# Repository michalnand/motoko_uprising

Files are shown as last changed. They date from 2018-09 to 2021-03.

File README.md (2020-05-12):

# Motoko Uprising
## line following robot with neural network predictor

Advanced line following robot, using custom deep neural network for curve shape prediction.
Robot can recognize straight line and speed up.

* Video1 of woking robot [motoko video 1](https://www.youtube.com/watch?v=E9FJIDowNmU)
* Video2 of woking robot [motoko video 2](https://www.youtube.com/watch?v=xUAJ1LA6Xwc)

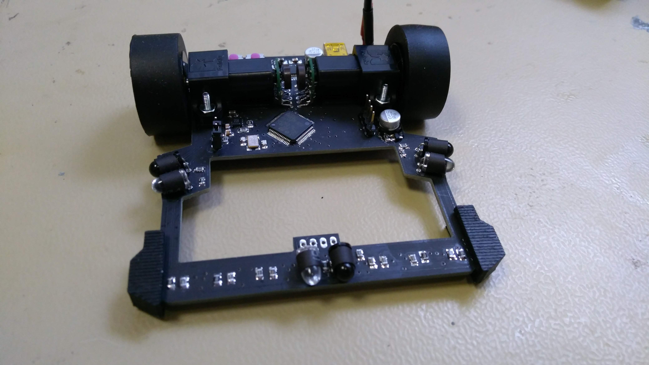
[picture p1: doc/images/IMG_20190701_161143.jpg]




## hardware

* CPU is ARM Cortex M4F, stm32f303, 72MHz
  * with simd instructions, good to have for deep learning
* gyroscope : lsm303 
  * (or something like THAT - yeah, they are changing it more often then socks)
* motors : pololu HP 1:30, micro metal gear, with magnetic encoders
* motor driver : TI DRV8834
* line sensors : phototransitors for visible light (not IR)
  * Iam using white leds, so the line can be colored - not only black
* obstacle detection :
  * common IR leds, and laser (still not working as I wish - too slow, but high range)
* accu : LiPol 2S, 150mAh, from dualsky

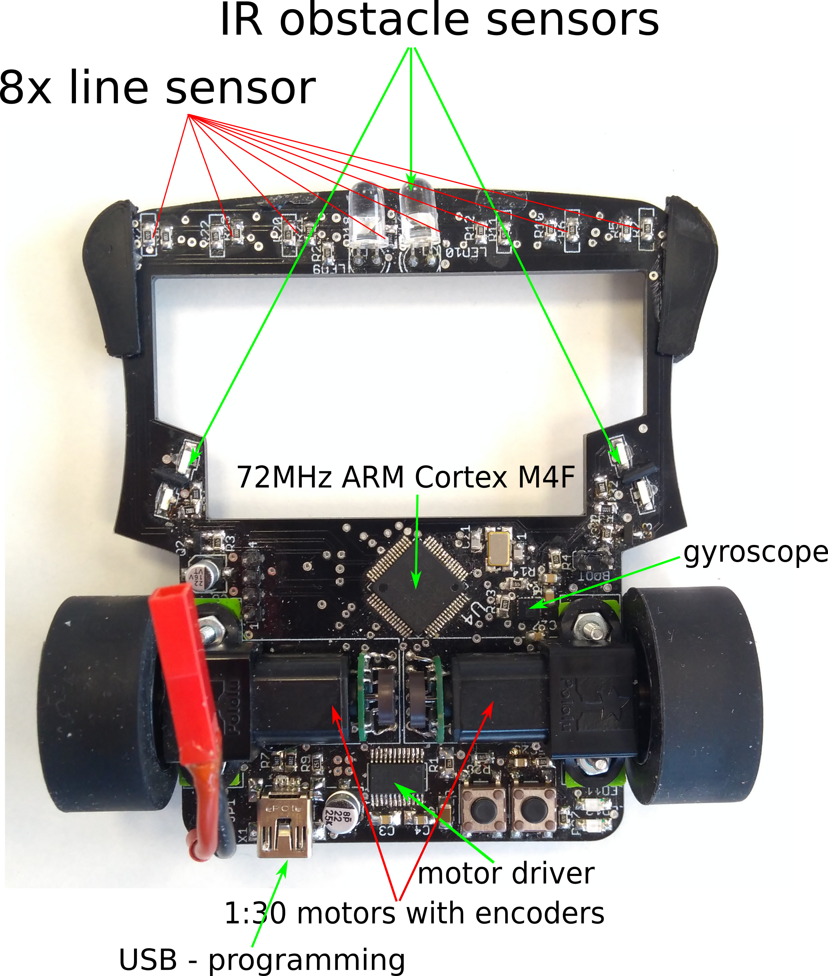
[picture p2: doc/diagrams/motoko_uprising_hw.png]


Some photos from mounting this devilry device :
* PCB design are in  [pcb](hardware/export), ready to send to your favorite manufactor
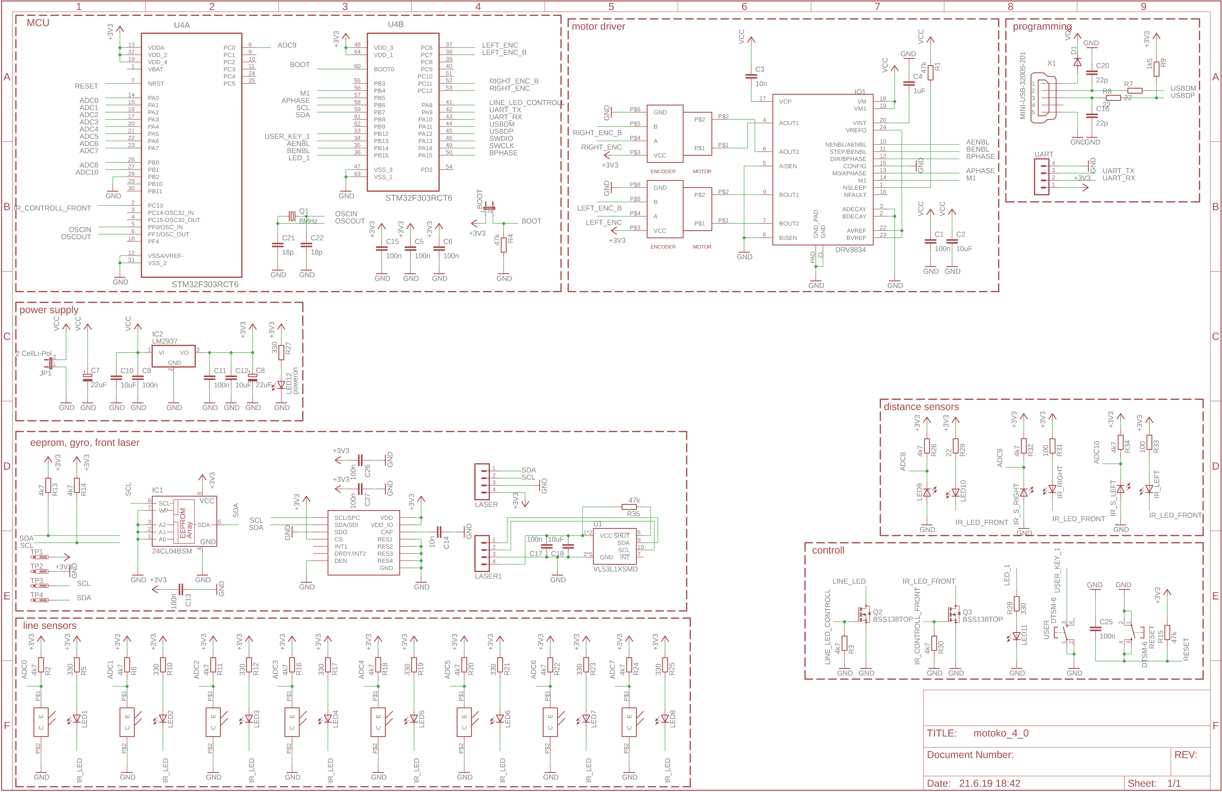
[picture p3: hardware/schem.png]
  * 
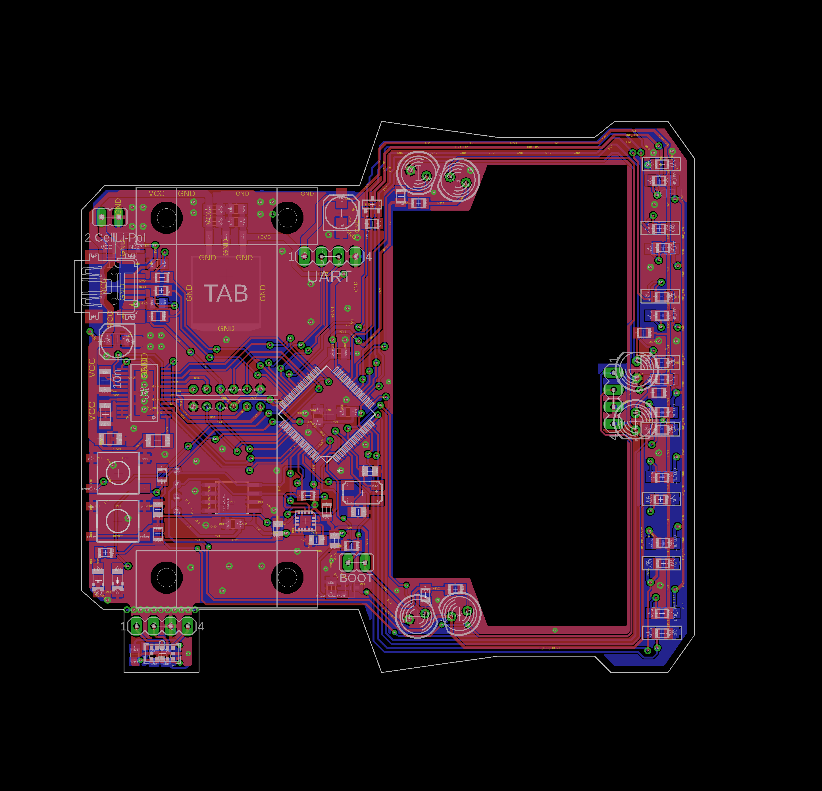
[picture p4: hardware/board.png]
  * 
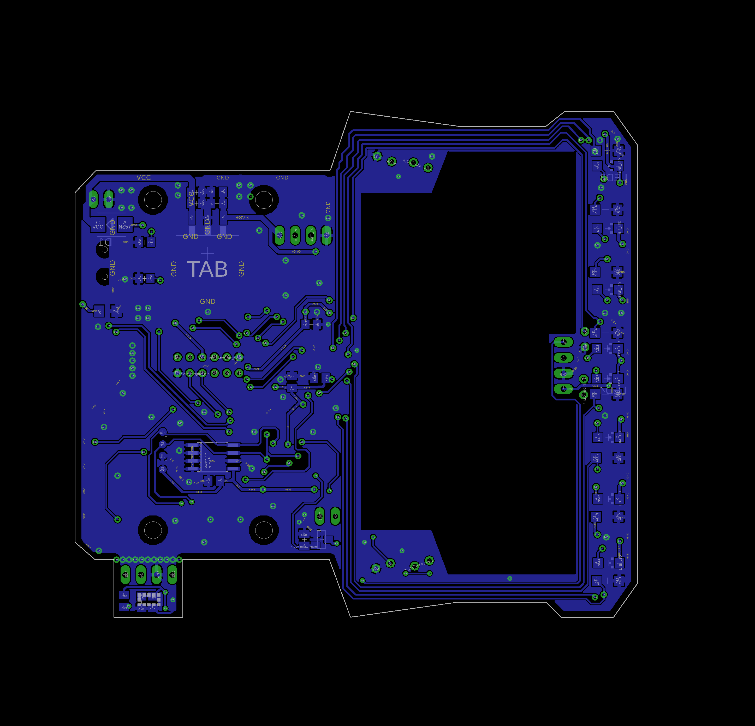
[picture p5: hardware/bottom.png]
  * 
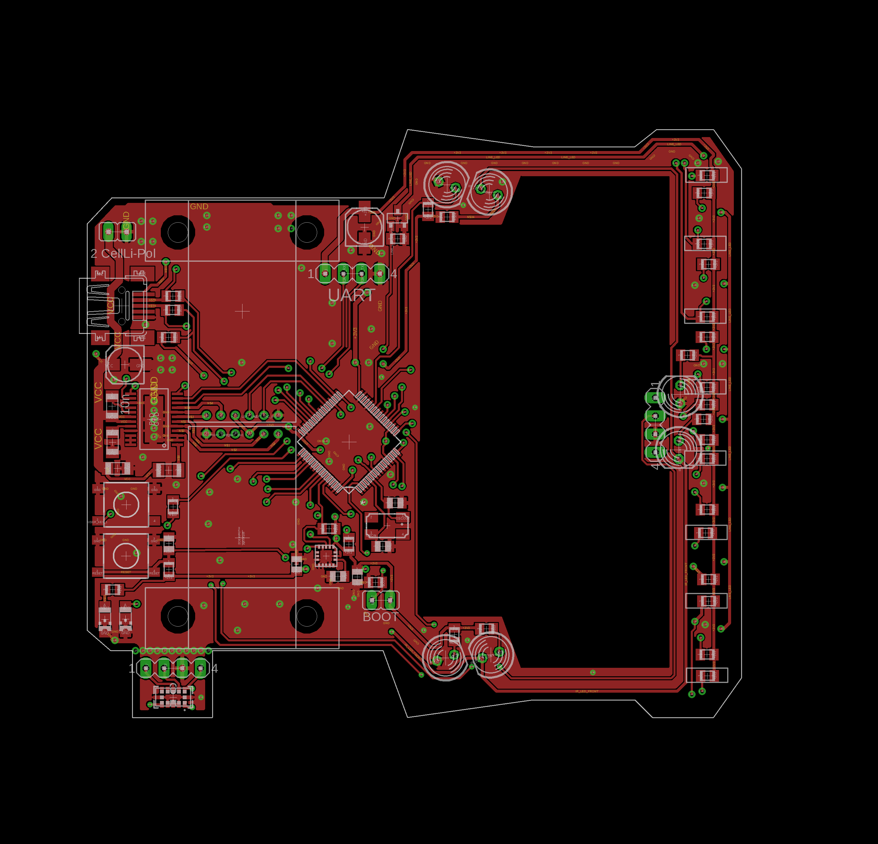
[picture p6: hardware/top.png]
  * 
  
* Chassis, there are little of 3D printed parts [3d print](hardware/chassis)
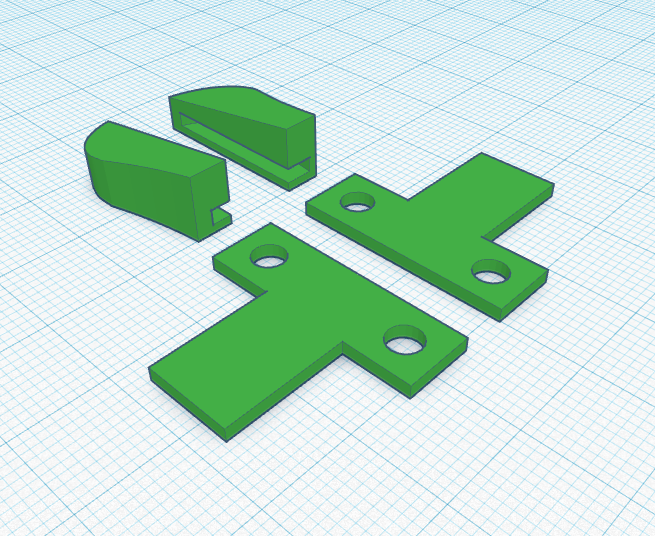
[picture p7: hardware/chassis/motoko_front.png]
  * 

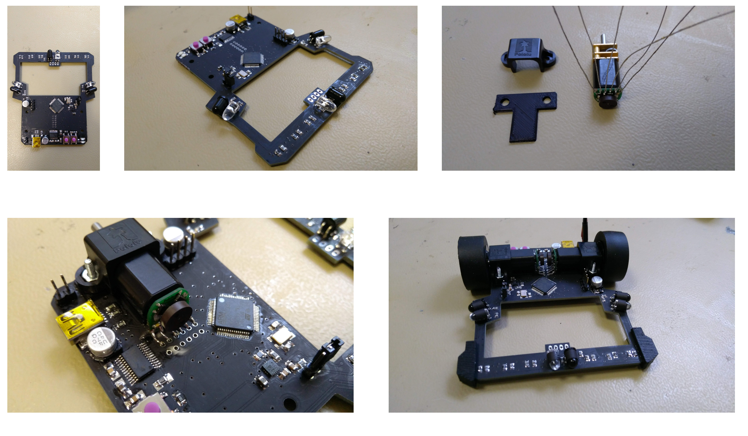
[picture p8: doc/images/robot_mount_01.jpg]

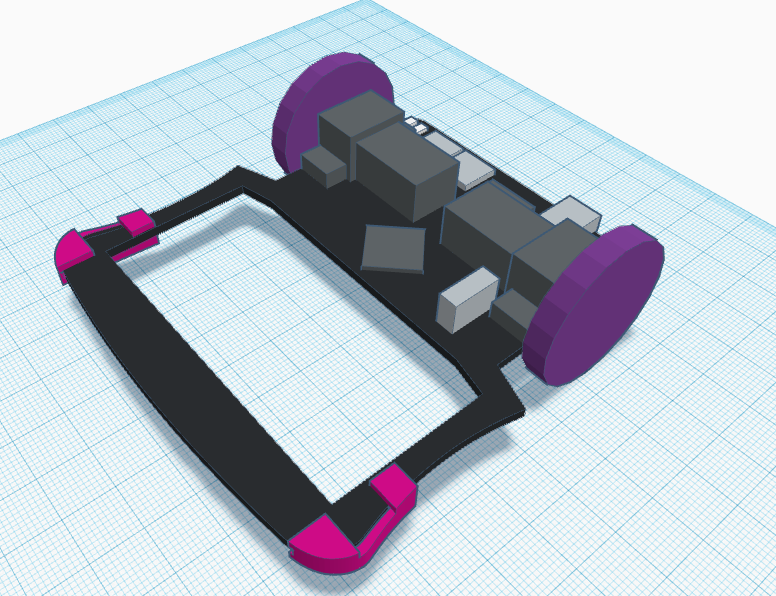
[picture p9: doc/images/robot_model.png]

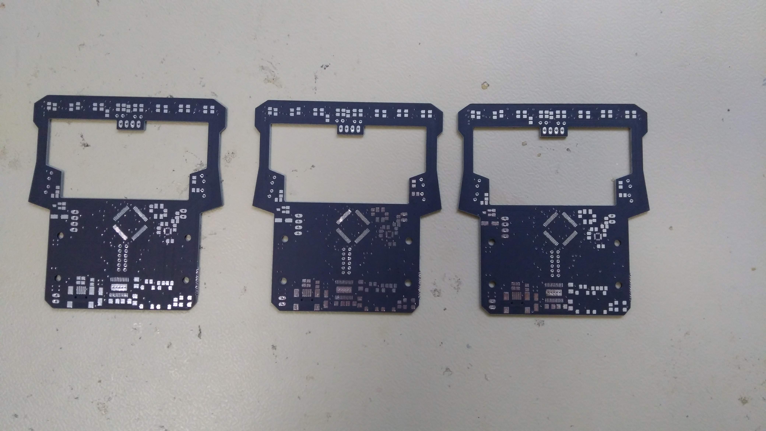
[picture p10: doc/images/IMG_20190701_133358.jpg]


## firmware

### control loops

* ADC reads line sensor, using quadratic interpolation for precission line position estimation
* for steering PD controller is used
* for motor controll two PIDs are used (data from encoders are filtered by low pass filters)
* target speed is estimated by neural network, using line shape classification

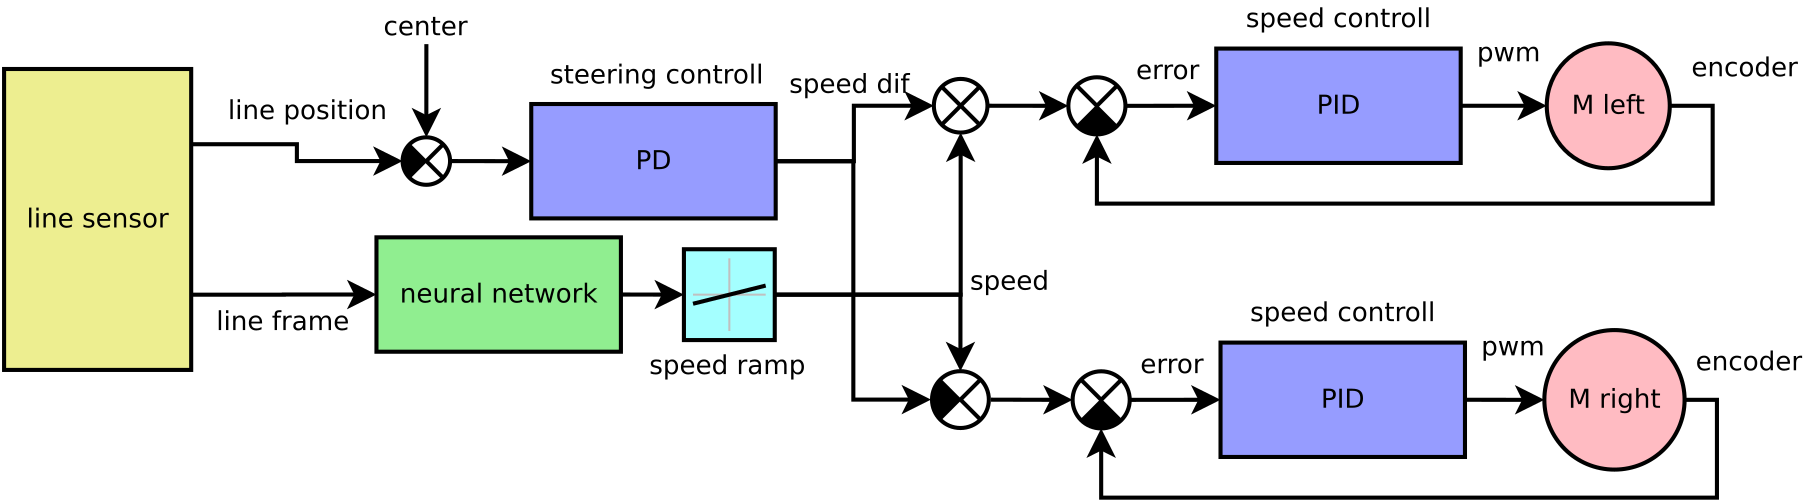
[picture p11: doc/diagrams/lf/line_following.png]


### neural network

tiny convolutional neural network is used, with architecture :
IN1x8x8 - C4x3x3 - P2x2 - C8x3x3 - P2x2 - FC5

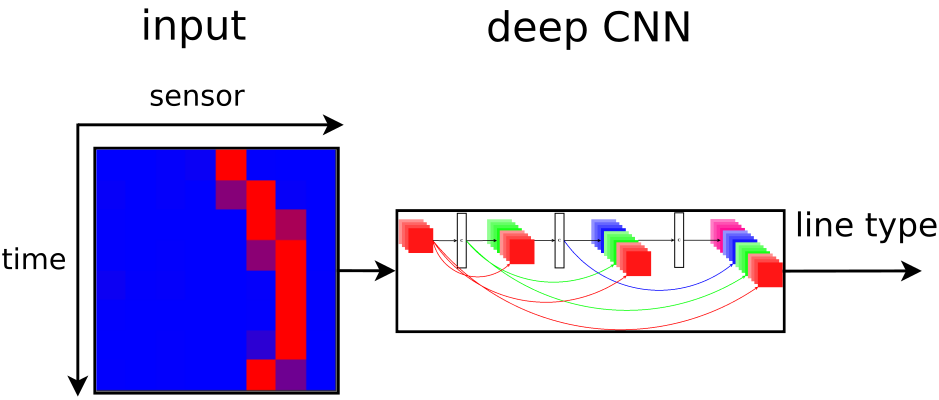
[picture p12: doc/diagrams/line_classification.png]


the custom embedded CNN framework is used

```cpp
LineNetwork::LineNetwork()
			:EmbeddedNet()
{
  input_shape.w = 8;
  input_shape.h = 8;
  input_shape.d = 1;

  output_shape.w = 1;
  output_shape.h = 1; 
  output_shape.d = 5;

  layers[0] = new EmbeddedNetConvolutionLayer(layer_0_shape,layer_0_input_shape,layer_0_output_shape,layer_0_weights,layer_0_bias,layer_0_weights_range,layer_0_bias_range);
  layers[1] = new EmbeddedNetMaxPoolingLayer(layer_1_shape,layer_1_input_shape,layer_1_output_shape);
  layers[2] = new EmbeddedNetConvolutionLayer(layer_2_shape,layer_2_input_shape,layer_2_output_shape,layer_2_weights,layer_2_bias,layer_2_weights_range,layer_2_bias_range);
  layers[3] = new EmbeddedNetMaxPoolingLayer(layer_3_shape,layer_3_input_shape,layer_3_output_shape);
  layers[4] = new EmbeddedNetFcLayer(layer_4_shape,layer_4_input_shape,layer_4_output_shape,layer_4_weights,layer_4_bias,layer_4_weights_range,layer_4_bias_range);

  layers_count = 5;
  allocate_buffer();
}
```

### PIDs

PIDs in differential form are used, with antiwindup and derivation kick avoid trick

the controller equation is :
u(n) = u(n-1) + k_0e(n) + k_1e(n-1) + k_2e(n-2)

where
* e(n) is error
* u(n) is controller output
* k0 = kp + ki + kd
* k1 = -kp     -2kd
* k2 = kd

```cpp
float PID::process(float error, float plant_output)
{
    e1 = e0;
    e0 = error;

    x2 = x1;
    x1 = x0;
    x0 = plant_output;

    u+= k0*e0 + k1*e1 - kd*(x0 - 2*x1 + x2);

    if (u > limit)
      u = limit;

    if (u < -limit)
      u = -limit;

    return u;
}
```

motors controllers step response :

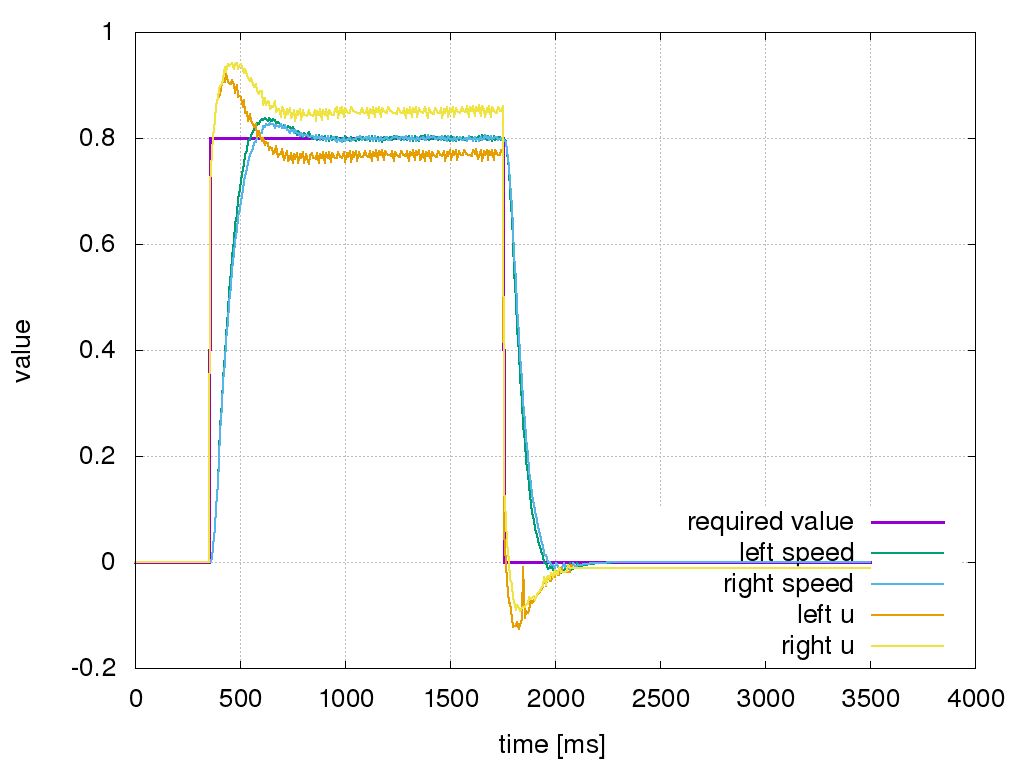
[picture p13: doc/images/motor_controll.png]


## debug application

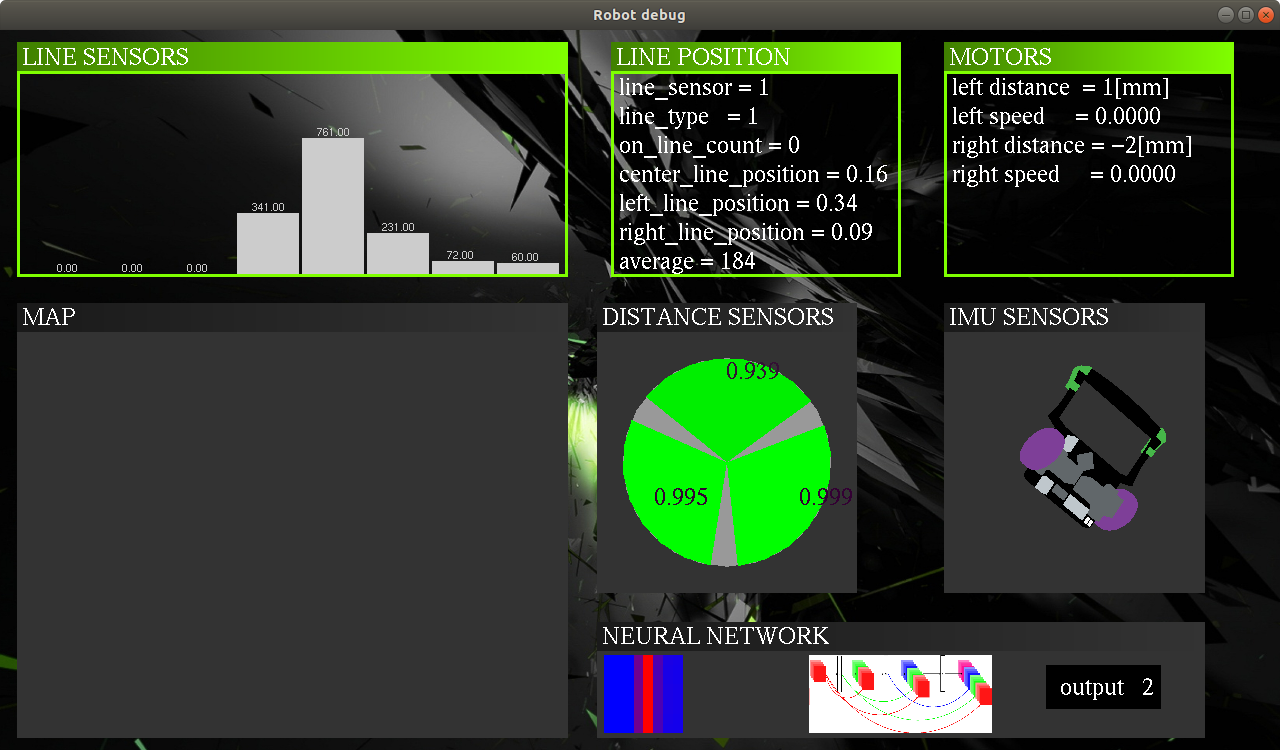
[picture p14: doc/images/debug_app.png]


There is debug application written in Python. Data received from robot are visualised in custom GUI written
using OpenGL. Data are transfered in JSON format.

Robot GUI is also designed in json - to modify gui design, only this file need to be modified. Example of gui.json file format : 

```json
"widgets" :
  {
    "type"      : "label",
    "position"  : [0.0, 0.0, 0.0],
    "color"     : [1.0, 0.0, 0.0],
    "font_size" : 0.1,

    "widgets" : [
                  {
                    "type"           : "bar_graph",
                    "position"       : [-2.0, 1.25, 0.0],
                    "color"          : [0.5, 1.0, 0.0],
                    "bar_color"      : [0.8, 0.8, 0.8],

                    "font_size" : 0.05,

                    "width"     : 1.5,
                    "height"    : 0.5,

                    "filled"    : false,
                    "enlight_max_value" : false,

                    "frame_width" : 0.01,
                    "label"     : "LINE SENSORS",

                    "min_value" : 0.0,
                    "max_value" : 1024.0,

                    "variable"  : {
                                    "name"  : "line_sensors",
                                    "value" : [3, 40, 500, 1000, 700, 50, 0, 0]
                                  }
                  },
...
```

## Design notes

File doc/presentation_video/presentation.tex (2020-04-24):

\documentclass[aspectratio=169]{beamer}
\usepackage[T1]{fontenc}
\usepackage[utf8]{inputenc}
\usepackage[english,slovak]{babel}

\usepackage{amsmath}
\usepackage{amsthm}
\usetheme{Pittsburgh}
\useoutertheme{shadow}

\usepackage{graphicx}
\usepackage{caption}
\usepackage{subcaption}

\usepackage[]{algorithm2e}
\usepackage{listings}
 \setbeamercovered{transparent}
 \usepackage{cuted}
\usepackage[export]{adjustbox}
\usepackage{mathtools}

\usepackage{lipsum}
\usepackage{verbatim}
\usepackage{transparent}
\usepackage{framed}
\usepackage{xcolor}

\usepackage{multirow}
\usepackage{colortbl}
\usepackage{lmodern}

\usepackage{movie15}

\newcommand\Wider[2][3em]{%
\makebox[\linewidth][c]{%
  \begin{minipage}{\dimexpr\textwidth+#1\relax}
  \raggedright#2
  \end{minipage}%
  }%
}

\iftrue

\usetheme{Warsaw}

\setbeamercolor{normal text}{fg=white,bg=black!90}
\setbeamercolor{structure}{fg=white}

\setbeamercolor{alerted text}{fg=red!85!black}

\setbeamercolor{item projected}{use=item,fg=black,bg=item.fg!35}

\setbeamercolor*{palette primary}{use=structure,fg=structure.fg}
\setbeamercolor*{palette secondary}{use=structure,fg=structure.fg!95!black}
\setbeamercolor*{palette tertiary}{use=structure,fg=structure.fg!90!black}
\setbeamercolor*{palette quaternary}{use=structure,fg=structure.fg!95!black,bg=black!80}

\setbeamercolor*{framesubtitle}{fg=white}

\setbeamercolor*{block title}{parent=structure,bg=black!60}
\setbeamercolor*{block body}{fg=black,bg=black!10}
\setbeamercolor*{block title alerted}{parent=alerted text,bg=black!15}
\setbeamercolor*{block title example}{parent=example text,bg=black!15}

\fi

%-------------------------------------------------------------------------------------

\setbeamertemplate{navigation symbols}{}
\setbeamertemplate{footline}{}

%\setbeamertemplate{footline}[frame number]{}

\setbeamersize{text margin left=2mm,text margin right=2mm} 

\date[EURP]{}
\begin{document}

{
    \usebackgroundtemplate
    {
        \vbox to \paperheight{\vfil\hbox to \paperwidth{\hfil

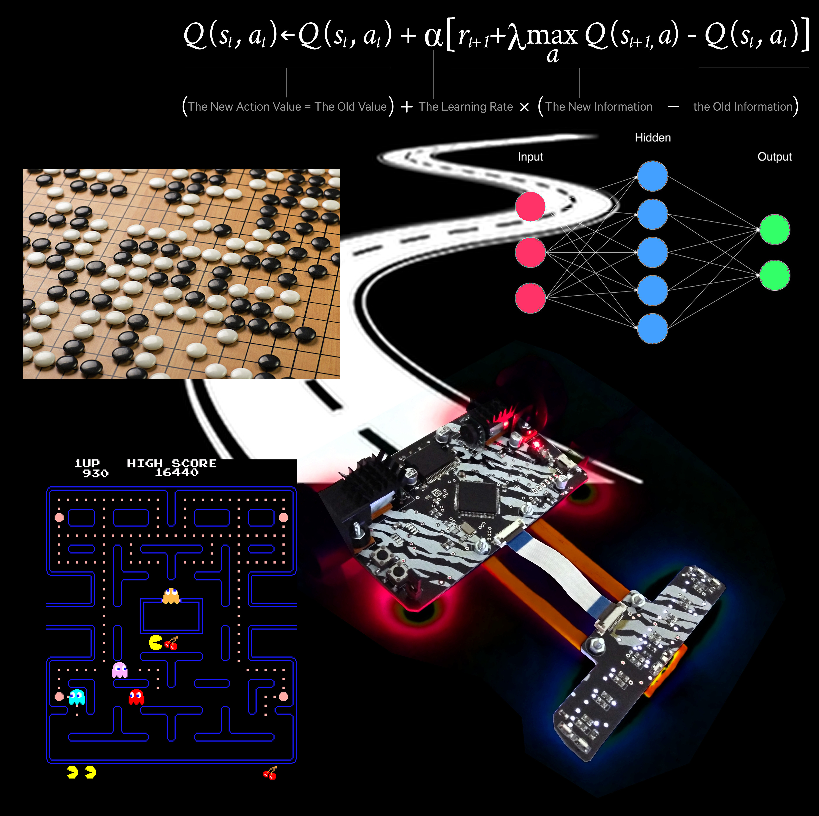
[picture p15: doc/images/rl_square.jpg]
        {}

        \hfil}\vfil}
    }
   
}

\begin{frame}{\bf \hfill fast line following}

\begin{columns}

    \begin{column}{0.55\textwidth}

    \end{column}

    \begin{column}{0.45\textwidth}

      \begin{itemize}
          \setlength\itemsep{5em}
          \item {\bf baseline}
            \begin{itemize}
              \item constant speed
              \item PD controller for steering
              \item PIDs for motors controll
            \end{itemize}

          \item {\bf neural network}
            \begin{itemize}
              \item automatic target speed estimating using convolutional neural network
              \item real time curve shape classification (200Hz)
              \item robot can accelerate on straight line
            \end{itemize}
      \end{itemize}

    \end{column}

\end{columns}

\end{frame}

\begin{frame}{\bf \hfill steering controll quality}

\begin{columns}

    \begin{column}{0.7\textwidth}

    \end{column}

    \begin{column}{0.3\textwidth}

      \begin{itemize}
          \setlength\itemsep{2em}
          \item PD controller for steering
          \item two PIDs for motors controll
      \end{itemize}

    \end{column}

\end{columns}

\end{frame}

\begin{frame}[t]{\bf \hfill other features}

\begin{columns}

    \begin{column}{0.7\textwidth}

    \end{column}

    \begin{column}{0.3\textwidth}

      \begin{itemize}
          \setlength\itemsep{1em}
          \item broken line search
          \item color line following
      \end{itemize}

       \vfill

    \end{column}

\end{columns}

\end{frame}

\begin{frame}{\bf hardware}

\begin{columns}

    \begin{column}{0.5\textwidth}

        \begin{figure}
            
        \end{figure}

    \end{column}

    \begin{column}{0.5\textwidth}

       \begin{itemize}
          \item MCU stm32f303, ARM Cortex M4F
            \begin{itemize}
              \item 72MHz
              \item 32bit floating point unit
              \item SIMD DSP instructions for deep learning
            \end{itemize}
          \item POLOLU micro metal gear motors
            \begin{itemize}
              \item gear ratio 1:30
              \item 180 pulses quadrature encoders
              \item DRV8834 H-Bridge driver
            \end{itemize}
          \item Sensors
            \begin{itemize}
              \item 8x phototransistor + white LED, 540nm
              \item 3xIR leds for obstacle detection
              \item gyroscope + accelerometer, LSM6DS0
            \end{itemize}
      \end{itemize}

    \end{column}

\end{columns}

\end{frame}

\begin{frame}{\bf 3D model for simulations}

  \begin{figure}
    
  \end{figure}

\end{frame}

\begin{frame}{\bf PCB - top layer}

  \begin{figure}
    
  \end{figure}

\end{frame}

\begin{frame}{\bf PCB - bottom layer}

  \begin{figure}
    
  \end{figure}

\end{frame}

\begin{frame}{\bf PCB - design}

  \begin{figure}
    
  \end{figure}

\end{frame}

\begin{frame}{\bf assembling process}

  \begin{figure}
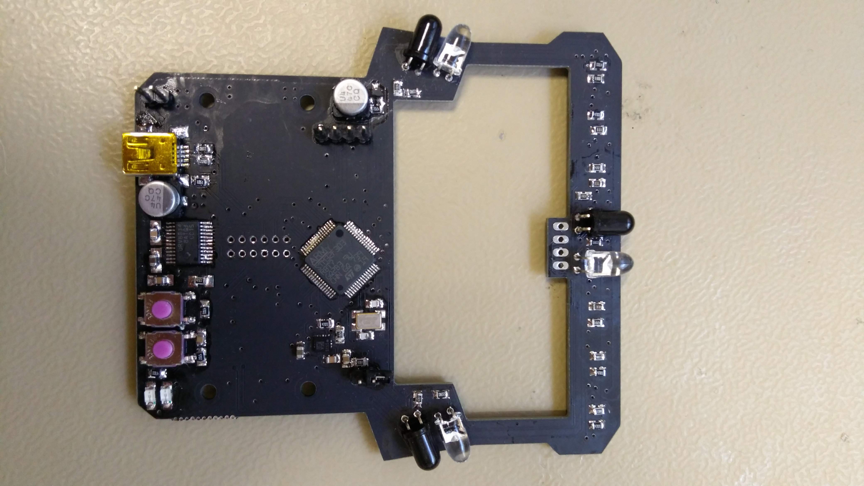
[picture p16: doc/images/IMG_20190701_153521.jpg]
    
  \end{figure}

\end{frame}

\begin{frame}{\bf assembling process - soldering detail}

  \begin{figure}
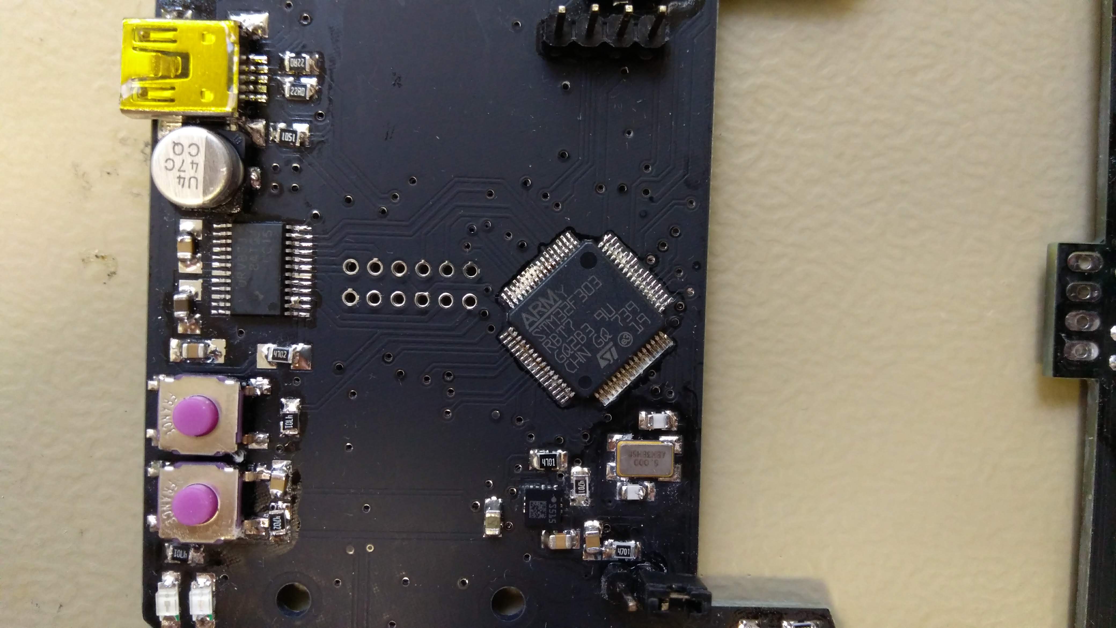
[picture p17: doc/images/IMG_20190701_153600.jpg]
    
  \end{figure}

\end{frame}

\begin{frame}{\bf assembling process - motor connection}

  \begin{figure}
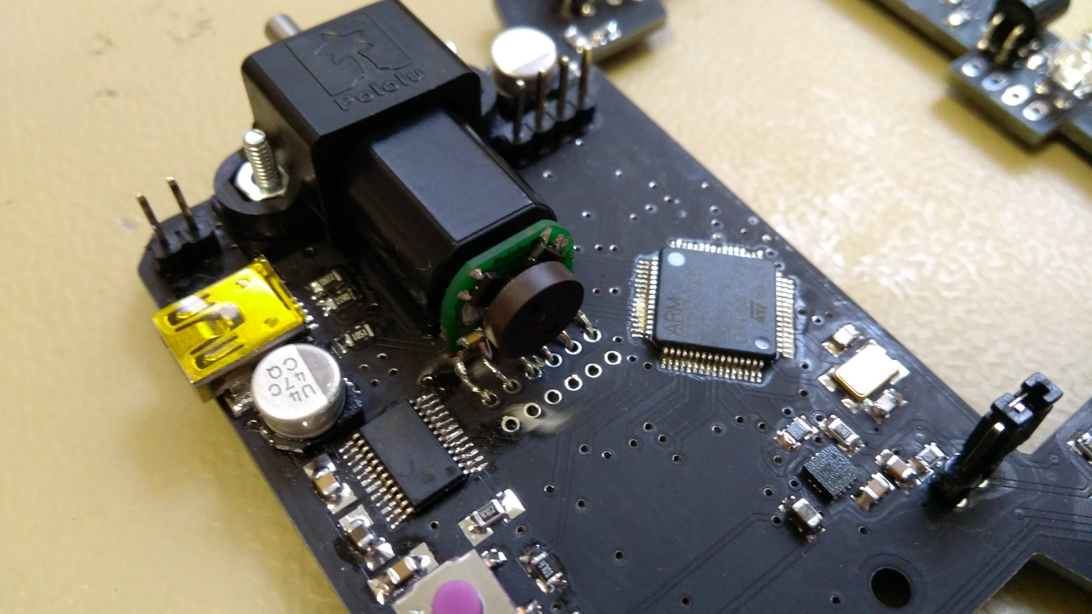
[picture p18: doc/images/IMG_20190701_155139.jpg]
    
  \end{figure}

\end{frame}

\begin{frame}{\bf assembling process - complete robot}

  \begin{figure}
    
  \end{figure}

\end{frame}

\begin{frame}{\bf software}

\begin{itemize}
  \item robot firmware is very complex - {\color{red} \bf thousands of lines} of C++ code
  \item there is custom C++11 templates {\color{red} hardware abstraction layer}
  \item custom {\color{red} event driven operating system} - all sensors tasks are running on background
  \item programmed without IDE, just simple text editor, \\
    {\color{red} sources are availible on} : \\
    https://github.com/michalnand/motoko\_uprising
\end{itemize}

\end{frame}

\begin{frame}[b]{\bf controll process}

  \vfill
  
  \begin{figure}[b!]
    
  \end{figure}

\end{frame}

\begin{frame}[b]{\bf controll process - sensor reading}

\begin{enumerate}
  \setcounter{enumi}{0}
  \item the {\color{red} \bf line sensors} are readed using ADC \\
\end{enumerate}

  \vfill

  \begin{figure}[b!]
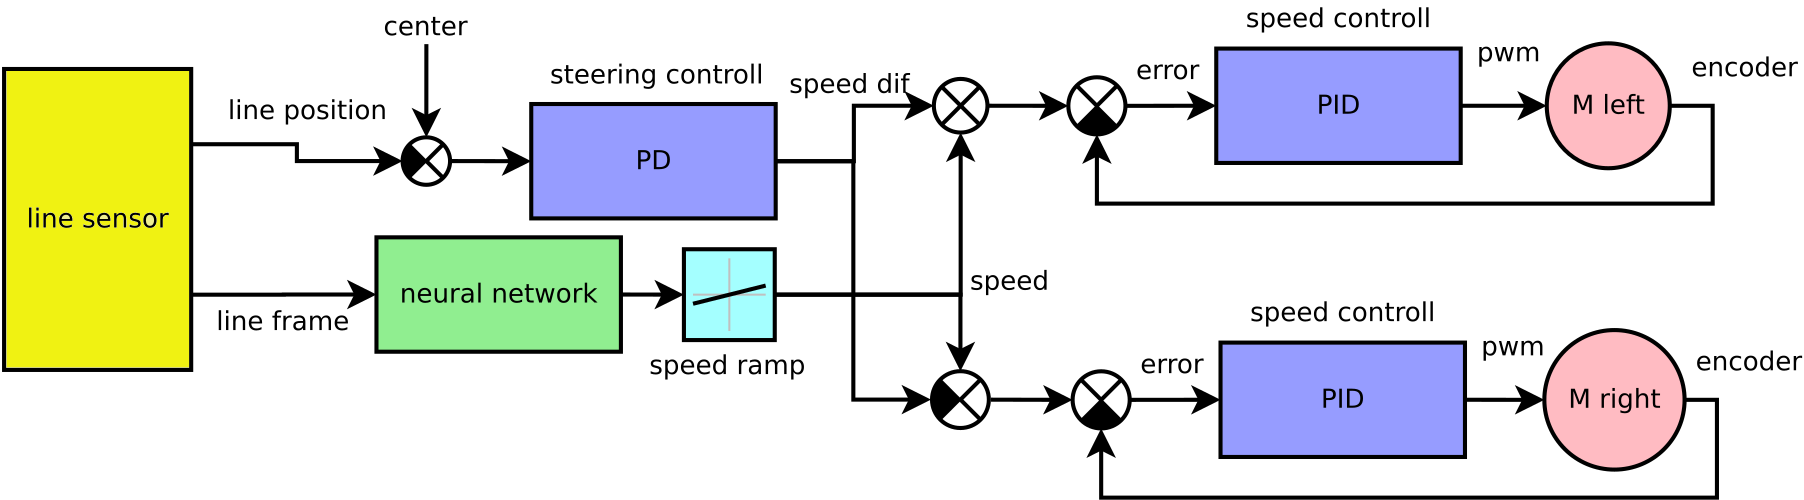
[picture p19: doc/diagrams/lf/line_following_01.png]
    
  \end{figure}

\end{frame}

\begin{frame}[b]{\bf controll process - sensor reading}

\begin{enumerate}
  \setcounter{enumi}{0}

  \item the {\color{red} \bf line sensors} are readed using ADC \\
    - thanks quadratic position interpolation, it provides 512 possible line positions
\end{enumerate}

  \vfill

  \begin{figure}[b!]
    
  \end{figure}

\end{frame}

\begin{frame}[b]{\bf controll process - neural network}

\begin{enumerate}
  \setcounter{enumi}{1} 
  \item the {\color{red} \bf neural network} performs curve shape classification
\end{enumerate}

 \vfill

  \begin{figure}
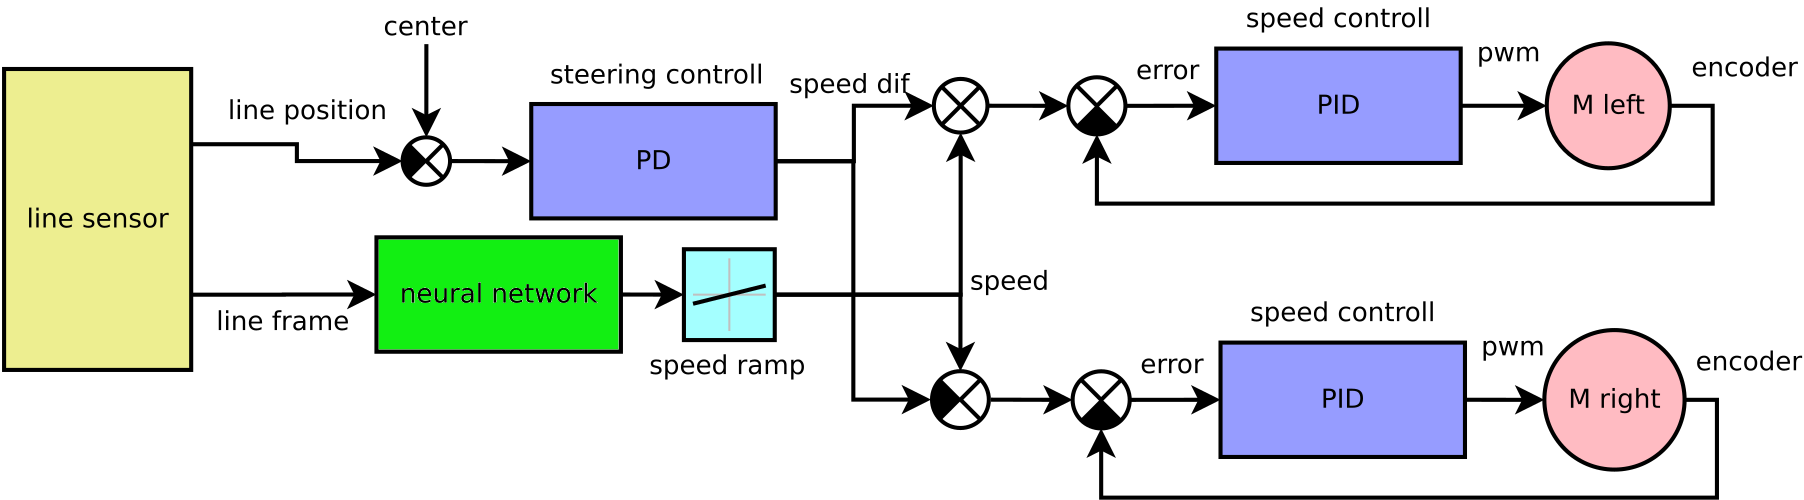
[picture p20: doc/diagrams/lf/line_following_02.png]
    
  \end{figure}

\end{frame}

\begin{frame}[b]{\bf controll process - neural network}

\begin{enumerate}
  \setcounter{enumi}{1}
  \item the {\color{red} \bf neural network} performs curve shape classification
    \begin{itemize}
      \item input is matrix, 8x8, eight past line sensors readings
      \item output is one of 5 classes : \\
        sharp left,  soft left, center line, soft right, or sharp right
      \item network runtime is only 2 miliseconds
    \end{itemize}
\end{enumerate}

 \vfill

 \begin{columns}

    \begin{column}{0.5\textwidth}

      \begin{figure}
        
      \end{figure}

    \end{column}

    \begin{column}{0.5\textwidth}

      \begin{figure}
        
      \end{figure}

    \end{column}

\end{columns}

\end{frame}

\begin{frame}[b]{\bf controll process - steering}

\begin{enumerate}
  \setcounter{enumi}{2}
  \item the {\color{red} \bf steering} PD controller compute speed difference
\end{enumerate}

 \vfill

  \begin{figure}
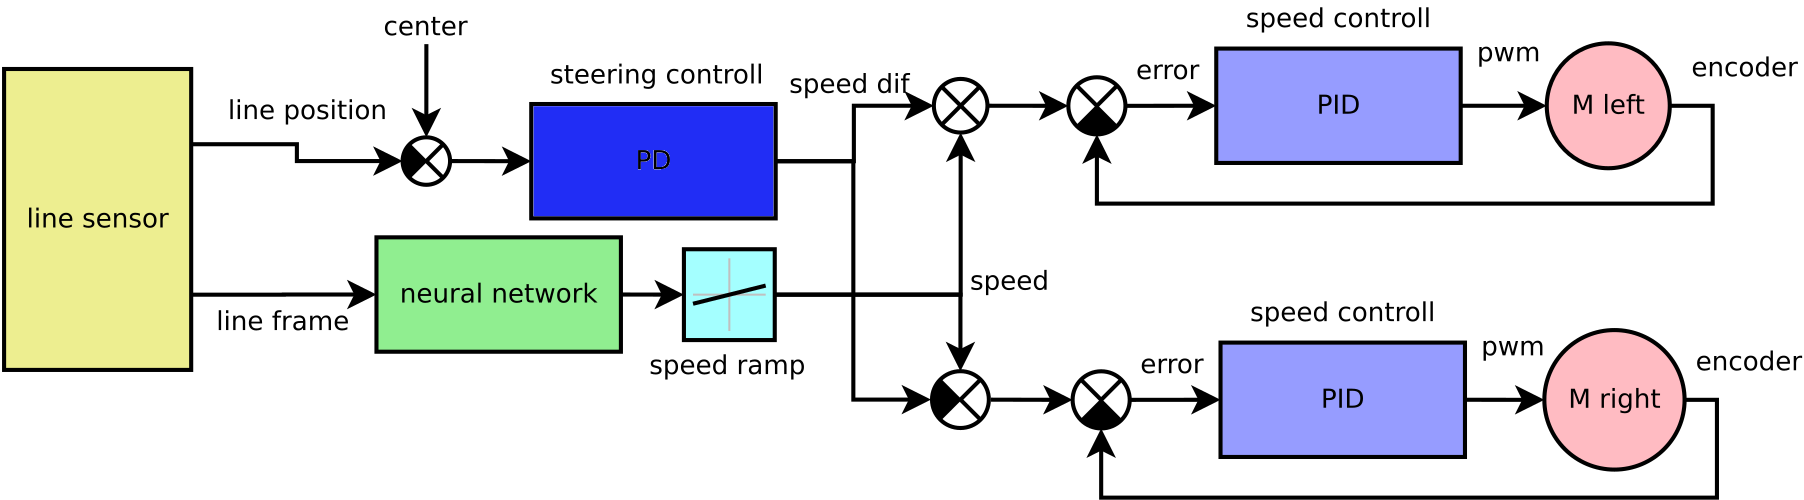
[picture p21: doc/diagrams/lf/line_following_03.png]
    
  \end{figure}

\end{frame}

\begin{frame}[b]{\bf controll process - steering}

\begin{enumerate}
  \setcounter{enumi}{2}
  \item the {\color{red} \bf steering} PD controller compute speed difference \\
    - of course, the filtered derivative term is used
\end{enumerate}

 \vfill

  \begin{figure}
    
  \end{figure}

\end{frame}

\begin{frame}[b]{\bf controll process - motors controll}

\begin{enumerate}
  \setcounter{enumi}{2}
  \item the {\color{red} \bf motors speed} is controlled with two PIDs
\end{enumerate}

 \vfill

  \begin{figure}
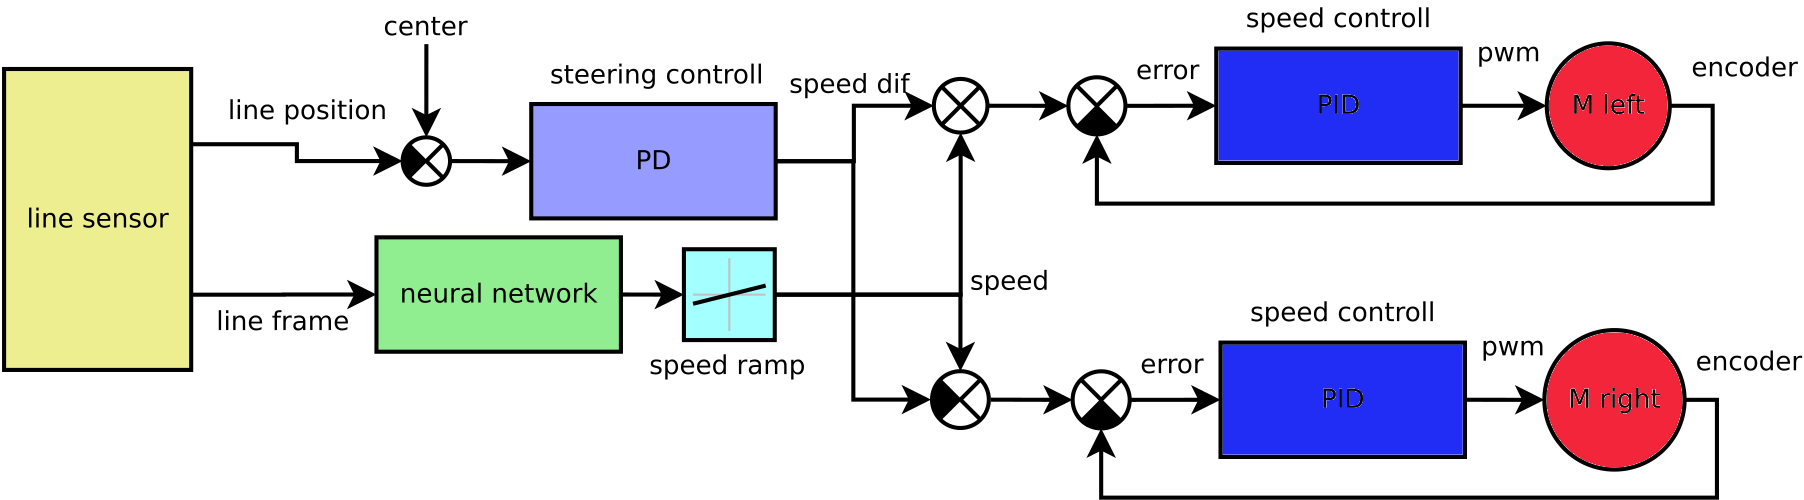
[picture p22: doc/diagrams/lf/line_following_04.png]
    
  \end{figure}

\end{frame}

\begin{frame}[b]{\bf controll process - motors controll}

\begin{enumerate}
  \setcounter{enumi}{2}
  \item the {\color{red} \bf motors speed} is controlled with two PIDs \\
    - PIDs are using antiwindup, so the response looks quick
\end{enumerate}

 \vfill

\begin{columns}

    \begin{column}{0.5\textwidth}

      \begin{figure}
        
      \end{figure}

    \end{column}

    \begin{column}{0.5\textwidth}

  \begin{figure}
    
  \end{figure}

    \end{column}

\end{columns}

\end{frame}

\begin{frame}[t]{\bf \hfill end to end line follower}

\begin{columns}

    \begin{column}{0.55\textwidth}

    \end{column}

    \begin{column}{0.45\textwidth}

      \begin{itemize}
          \setlength\itemsep{0.5em}
          \item {\bf \color{red} reinforcement learning} line follower
      \end{itemize}

       \vfill

    \end{column}

\end{columns}

\end{frame}

\begin{frame}[t]{\bf \hfill end to end line follower}

\begin{columns}

    \begin{column}{0.55\textwidth}

    \end{column}

    \begin{column}{0.45\textwidth}

      \begin{itemize}
          \setlength\itemsep{0.5em}
          \item {\bf \color{red} reinforcement learning} line follower
          \item {\bf \color{red} no PD, PIDs, no dataset} \\ 
          -just learned from rewards and pushments
      \end{itemize}

       \vfill

    \end{column}

\end{columns}

\end{frame}

\begin{frame}[t]{\bf \hfill end to end line follower}

\begin{columns}

    \begin{column}{0.55\textwidth}

    \end{column}

    \begin{column}{0.45\textwidth}

      \begin{itemize}
          \setlength\itemsep{0.5em}
          \item {\bf \color{red} reinforcement learning} line follower
          \item {\bf \color{red} no PD, PIDs, no dataset} \\ 
          -just learned from rewards and pushments
          \item {\bf \color{red} self understand} what the line is, what the goal is ...
      \end{itemize}

       \vfill

    \end{column}

\end{columns}

\end{frame}

\begin{frame}[t]{\bf \hfill end to end line follower}

\begin{columns}

    \begin{column}{0.55\textwidth}

    \end{column}

    \begin{column}{0.45\textwidth}

      \begin{itemize}
          \setlength\itemsep{0.5em}
          \item {\bf \color{red} reinforcement learning} line follower
          \item {\bf \color{red} no PD, PIDs, no dataset} \\ 
          -just learned from rewards and pushments
          \item {\bf \color{red} self understand} what the line is, what the goal is ...
          \item {\bf \color{red} advantage actor critic} algorithm
      \end{itemize}

       \vfill

    \end{column}

\end{columns}

\end{frame}

\begin{frame}[t]{\bf \hfill end to end line follower}

\begin{columns}

    \begin{column}{0.55\textwidth}

    \end{column}

    \begin{column}{0.45\textwidth}

      \begin{itemize}
          \setlength\itemsep{0.5em}
          \item {\bf \color{red} reinforcement learning} line follower
          \item {\bf \color{red} no PD, PIDs, no dataset} \\ 
          -just learned from rewards and pushments
          \item {\bf \color{red} self understand} what the line is, what the goal is ...
          \item {\bf \color{red} advantage actor critic} algorithm
          \item here is the magic 
            \begin{align*} 
              \mathcal{L} = &(V - \hat{V})^2 + \\
                     &-log(p(A|S))(V - \hat{V}) \\
                     &-\beta \mathcal{H}(A)
            \end{align*}
      \end{itemize}

       \vfill

    \end{column}

\end{columns}

\end{frame}

\begin{frame}{}

\centering
{\bf Thanks for watching}

\end{frame}

\end{document}

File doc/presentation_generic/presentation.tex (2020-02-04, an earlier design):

\documentclass[xcolor=dvipsnames]{beamer}
\usepackage[T1]{fontenc}
\usepackage[utf8]{inputenc}
\usepackage[english,slovak]{babel}

\usepackage{amsmath}
\usepackage{amsthm}
\usetheme{Pittsburgh}
\useoutertheme{shadow}

\usepackage{graphicx}
\usepackage{caption}
\usepackage{subcaption}

\usepackage[]{algorithm2e}
\usepackage{listings}
 \setbeamercovered{transparent}
 \usepackage{cuted}
\usepackage[export]{adjustbox}
\usepackage{mathtools}

\usepackage{lipsum}
\usepackage{verbatim}
\usepackage{transparent}
\usepackage{framed}
\usepackage{xcolor}

\usepackage{multirow}
\usepackage{colortbl}
\usepackage{lmodern}

\usepackage{movie15}

\newcommand\Wider[2][3em]{%
\makebox[\linewidth][c]{%
  \begin{minipage}{\dimexpr\textwidth+#1\relax}
  \raggedright#2
  \end{minipage}%
  }%
}

\iftrue

\usetheme{Warsaw}

\setbeamercolor{normal text}{fg=white,bg=black!90}
\setbeamercolor{structure}{fg=white}

\setbeamercolor{alerted text}{fg=red!85!black}

\setbeamercolor{item projected}{use=item,fg=black,bg=item.fg!35}

\setbeamercolor*{palette primary}{use=structure,fg=structure.fg}
\setbeamercolor*{palette secondary}{use=structure,fg=structure.fg!95!black}
\setbeamercolor*{palette tertiary}{use=structure,fg=structure.fg!90!black}
\setbeamercolor*{palette quaternary}{use=structure,fg=structure.fg!95!black,bg=black!80}

\setbeamercolor*{framesubtitle}{fg=white}

\setbeamercolor*{block title}{parent=structure,bg=black!60}
\setbeamercolor*{block body}{fg=black,bg=black!10}
\setbeamercolor*{block title alerted}{parent=alerted text,bg=black!15}
\setbeamercolor*{block title example}{parent=example text,bg=black!15}

\fi

%-------------------------------------------------------------------------------------

\title{\bf DL linefollower}
\author{Michal CHOVANEC, PhD}

\setbeamertemplate{navigation symbols}{}
\setbeamertemplate{footline}[frame number]{}

\date[EURP]{}
\begin{document}

{
    \usebackgroundtemplate
    {
        \vbox to \paperheight{\vfil\hbox to \paperwidth{\hfil

        {}

        \hfil}\vfil}
    }
    \begin{frame}

    %\titlepage

    \centering
     \colorbox{black}
     {
        \begin{minipage}{7cm}
           {\LARGE \color{white} \bf deep learning \\ for line following robot} \\
           {\LARGE \color{white} Michal CHOVANEC} \\
       \end{minipage}
     }

    \end{frame}
}

\begin{frame}{\bf line follower competition}

    \centering
    \includemovie[
      poster,
      autoplay,
      externalviewer,
      inline=false,
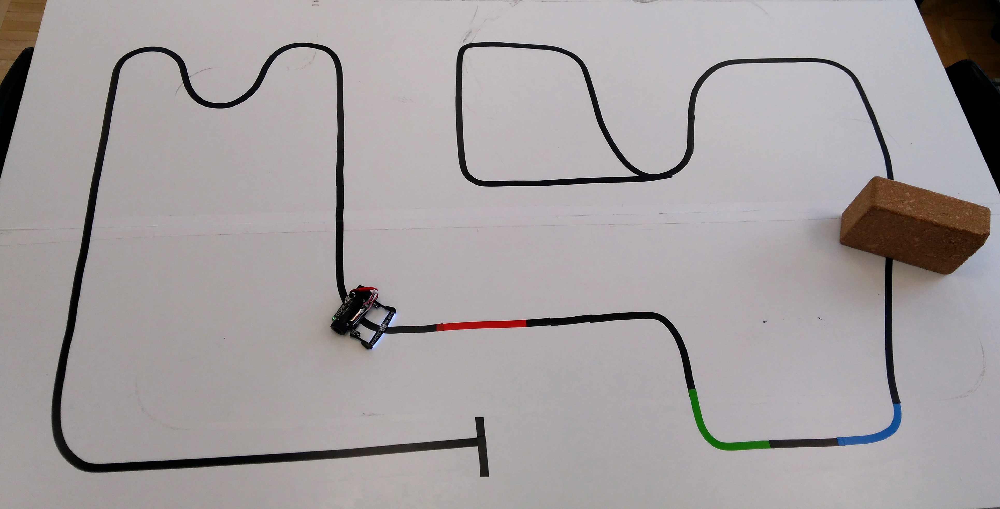
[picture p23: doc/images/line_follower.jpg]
      text={  }
    ]{9.5cm}{5cm}{../video/motoko_neural_network_test.mp4}

\begin{itemize}
    \item SR - Istrobot
    \item CR - Roboticky den
    \item AU - Robot Challenge
    \item PL - Zawody robotow
\end{itemize}

\end{frame}

\begin{frame}{\bf what does it take}

\begin{columns}

    \begin{column}{0.5\textwidth}

        \begin{itemize}
            \item Hardware
                \begin{itemize}
                    \item strong light motors
                    \item high adhesion tyres
                    \item light accumulator
                    \item fast CPU
                    \item dozen of sensors
                \end{itemize}
            \item Software
                \begin{itemize}
                    \item hard real time OS
                    \item tunned PIDs
                    \item predictive controll
                    \item mapping
                \end{itemize}
        \end{itemize}

    \end{column}

    \begin{column}{0.5\textwidth}

        \begin{figure}
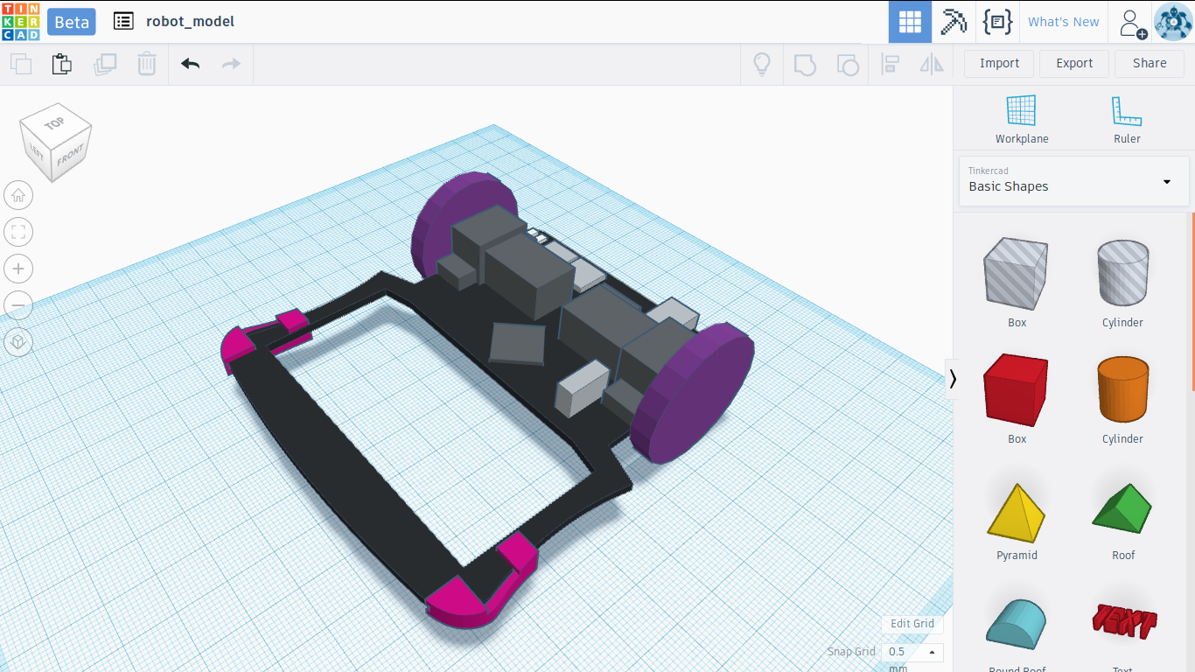
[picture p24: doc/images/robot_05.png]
            
        \end{figure}

        \begin{figure}
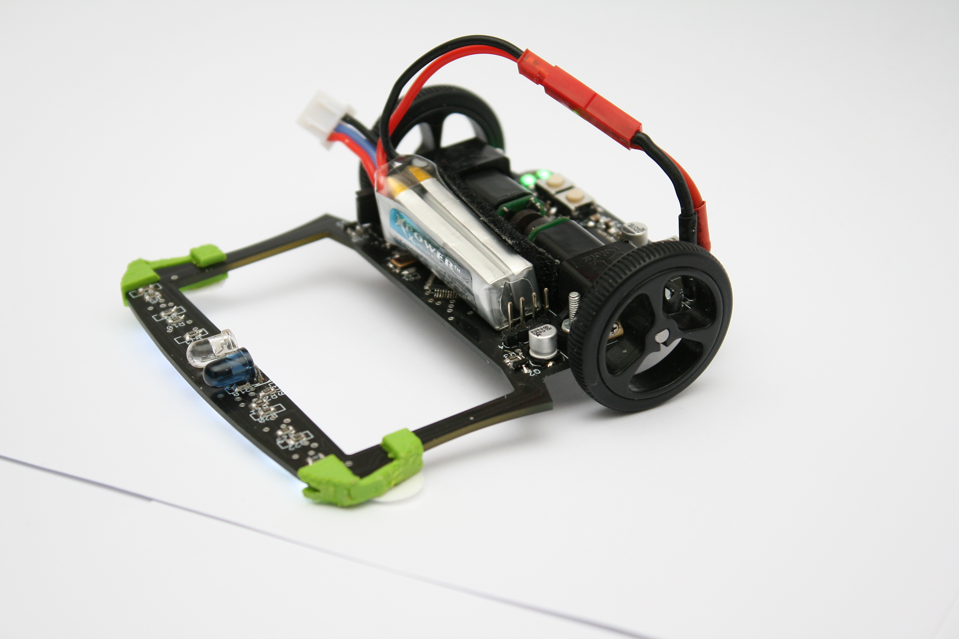
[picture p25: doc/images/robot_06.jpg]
            
        \end{figure}
 
    \end{column}

\end{columns}

\end{frame}

\begin{frame}{\bf motoko uprising - hardware}

\begin{columns}

    \begin{column}{0.5\textwidth}

        \begin{figure}
            
        \end{figure}

    \end{column}

    \begin{column}{0.5\textwidth}  %%<--- here
    {\small
        \begin{itemize}
            \item {\bf mcu}  : STM32F303, 72MHz ARM Cortex M4F
            \item {\bf motor driver} : TI DRV8834
            \item {\bf motors} : 1:30 HP Pololu, with magnetic encoder
            \item {\bf tyres} : Pololu 28mm diameter
            \item {\bf line sensor} : 8x 540nm phototransistor + white LED
            \item {\bf obstacle sensor} : SMD IR phototransistor + IR LED
            \item {\bf imu} : LSM6DS0, gyroscope + accelerometer
        \end{itemize}
    }
    \end{column}

\end{columns}

\end{frame}

\begin{frame}{\bf motoko uprising - hardware}

\begin{figure}
  
\end{figure}

\end{frame}

\begin{frame}{\bf software}

\begin{columns}

    \begin{column}{0.5\textwidth}  %%<--- here
    {\small
        \begin{itemize}
            \item {\bf quadratic interpolation}  : high precission line position computing
            \item {\bf steering PID}  : PD controller for steering
            \item {\bf motor PID}  : two PIDs for motors speed controll
            \item {\bf curve shape prediction}
                \begin{itemize}
                    \item {\bf fast} run on straight line, {\bf brake} on curve
                    \item {\color{red} \bf deep neural network}
                \end{itemize}
            \item written in {\bf C++}
            \item {\bf network training} on GPU - own framework for CNN
        \end{itemize}
    }
    \end{column}

    \begin{column}{0.5\textwidth}

        \begin{figure}
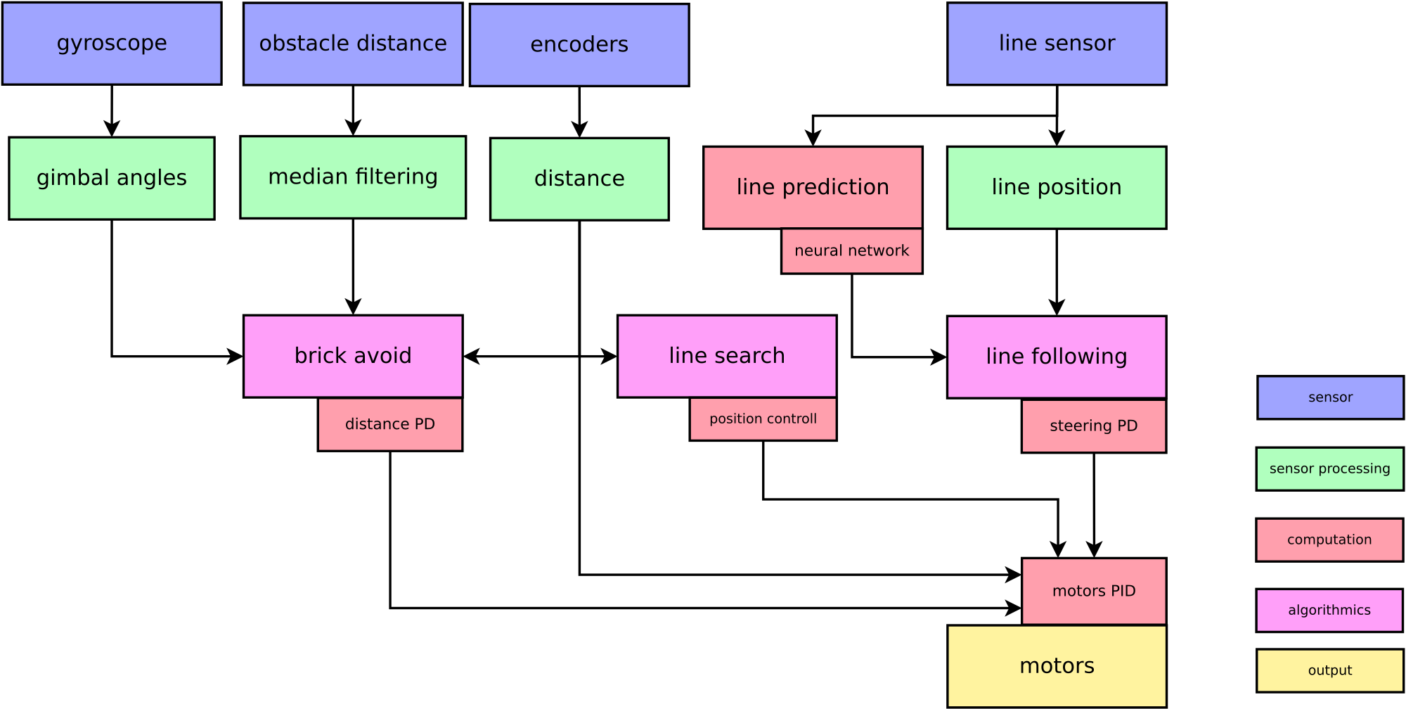
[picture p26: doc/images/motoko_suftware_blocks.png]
            
        \end{figure}

    \end{column}

\end{columns}

\end{frame}

\begin{frame}{\bf controll loop(s)}
        \begin{figure}
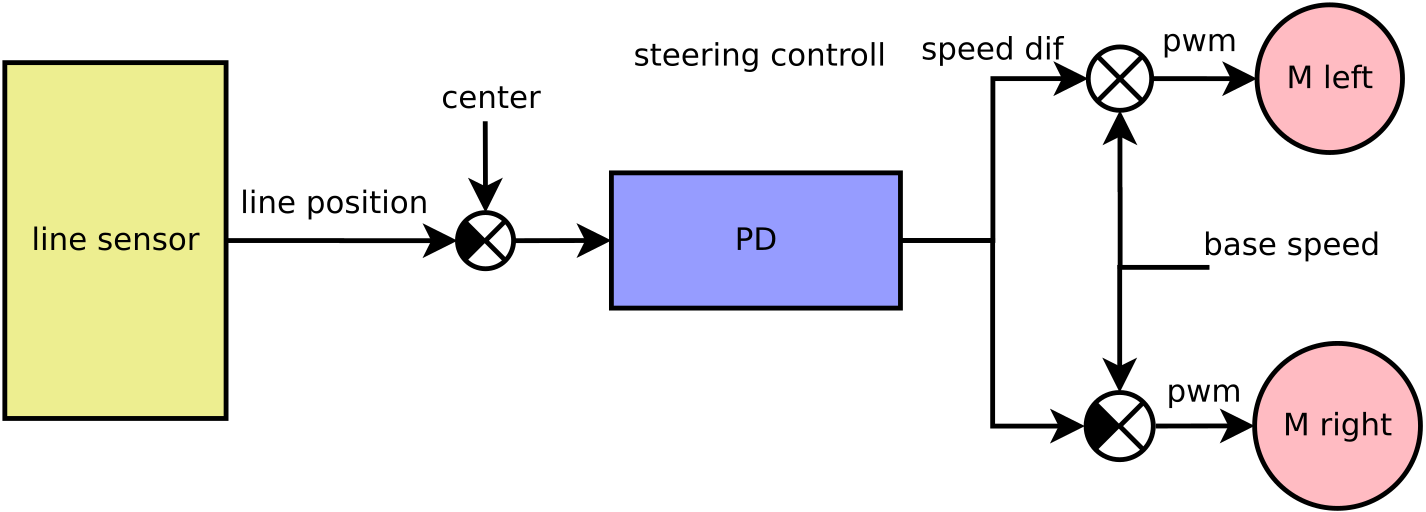
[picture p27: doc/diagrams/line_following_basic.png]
            
        \end{figure}
        
        \begin{figure}
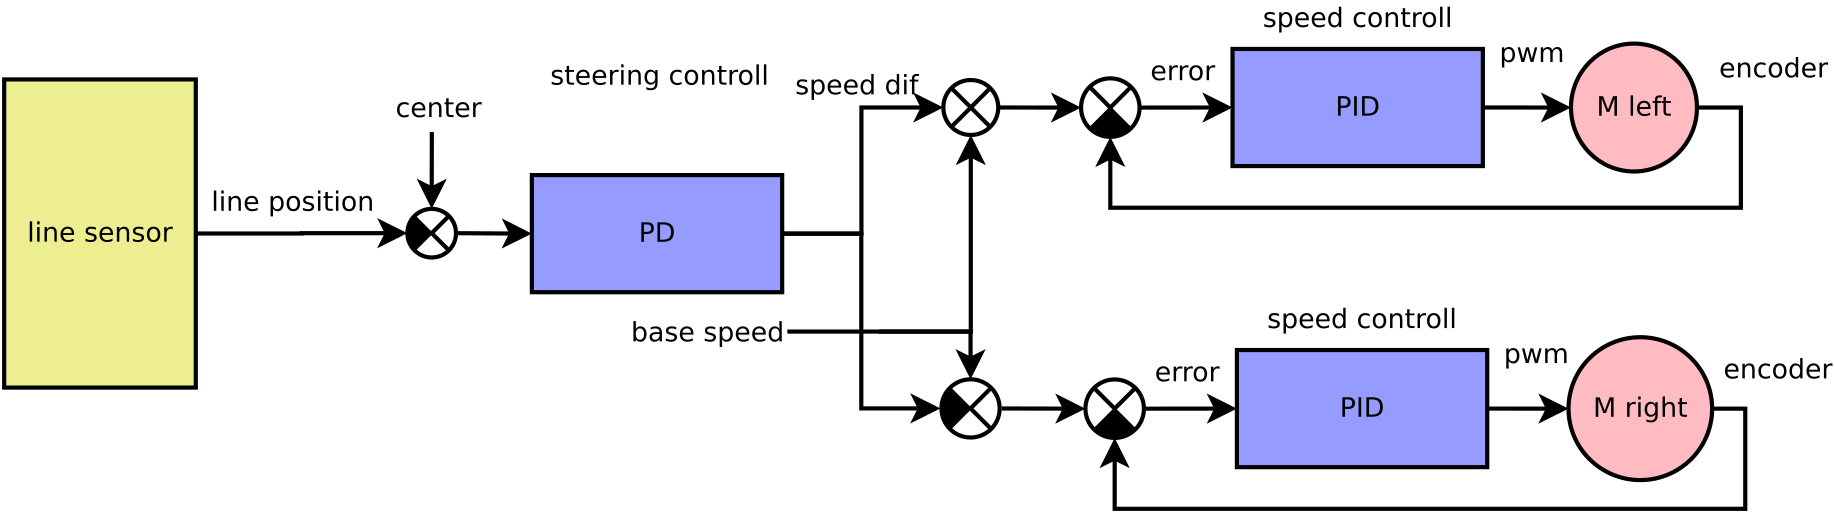
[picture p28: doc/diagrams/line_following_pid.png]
            
        \end{figure}
\end{frame}

\begin{frame}{\bf controll loop(s)}
        \begin{figure}
            
        \end{figure}
\end{frame}

\begin{frame}{\bf line shape prediction}

\begin{itemize}
    \item {\bf fast} run on straight line, {\bf brake} on curve
    \item {\bf neural network} for line type classification
        \begin{itemize}
            \item DenseNet - densely connected convolutional neural network
        \end{itemize}
    \item {\bf input} 8x8 matrix raw data from line sensors
        \begin{itemize}
            \item 8 past line positions from 8 sensors
        \end{itemize}
    \item {\bf output} 5 curves types
\end{itemize}

\centering
    \includemovie[
      poster,
      autoplay,
      externalviewer,
      inline=false,
      text={  }
    ]{8cm}{3.5cm}{../video/robot_line_cnn_out.mp4}

\end{frame}

\begin{frame}{\bf line dataset}

\begin{columns}

\begin{column}{0.5\textwidth}

    \begin{figure}
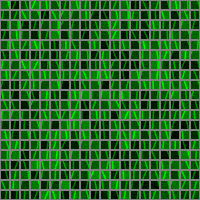
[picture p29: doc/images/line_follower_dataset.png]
        
    \end{figure}

\end{column}

\begin{column}{0.5\textwidth}  %%<--- here
{\small
    \begin{itemize}
        \item 20000 for training
        \item 2500 for testing
        \item 8x8 inputs
        \item 5 outputs (5 curves types)
            \begin{itemize}
                \item two left
                \item one straight
                \item two right
            \end{itemize}
        \item augmentation - luma noise, white noise

    \end{itemize}
}
\end{column}

\end{columns}

\end{frame}

\begin{frame}{\bf convolutional neural network - CNN}

  \begin{figure}
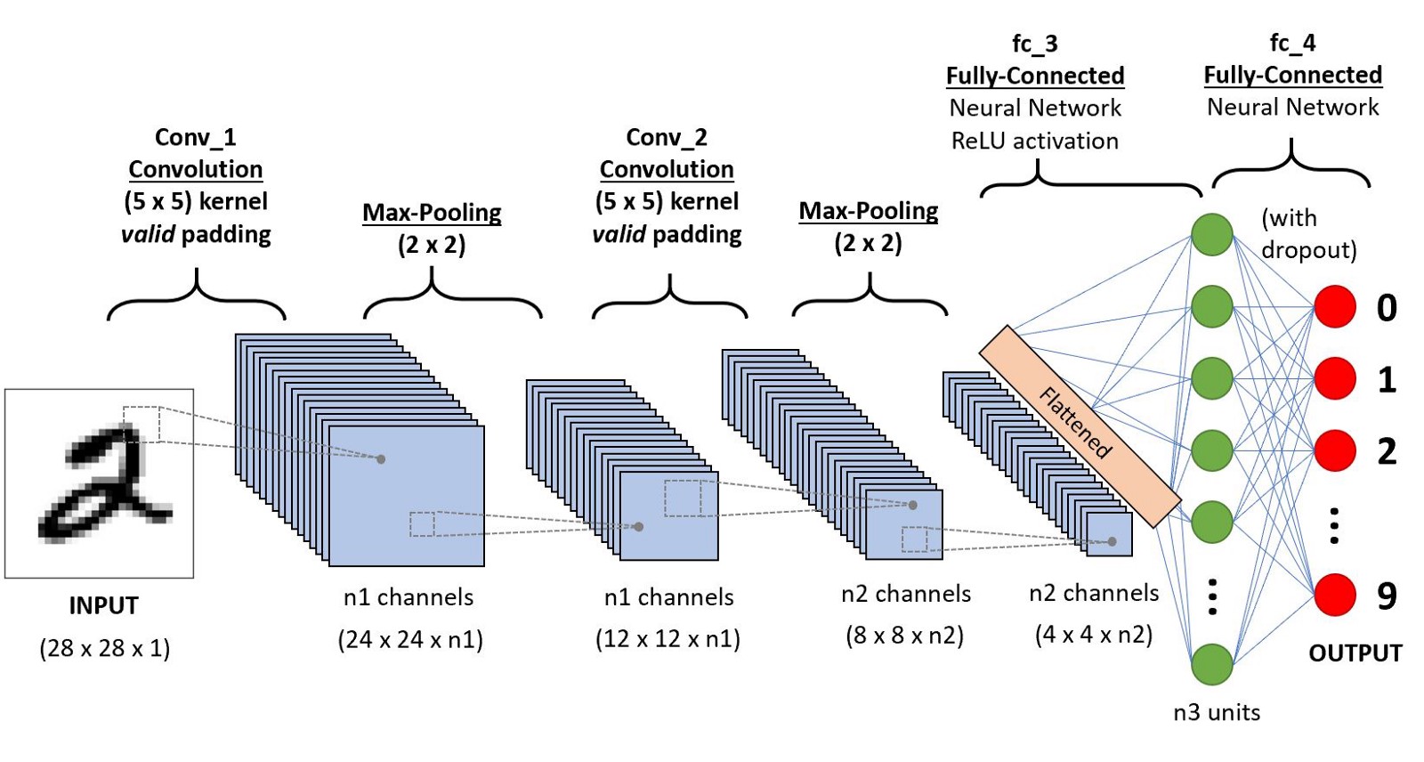
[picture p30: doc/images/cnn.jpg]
    
  \end{figure}

\end{frame}

\begin{frame}[fragile]
{\bf discrete convolution}

\begin{figure}
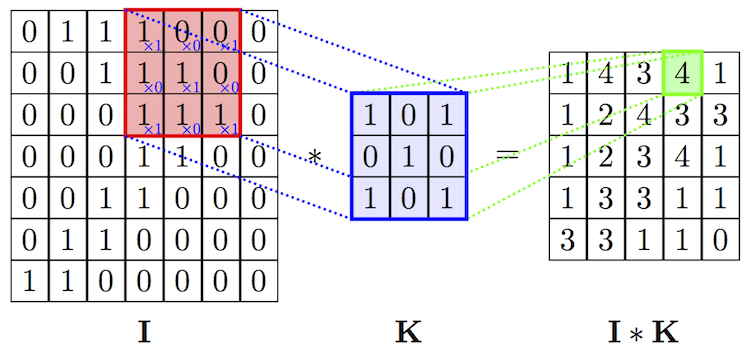
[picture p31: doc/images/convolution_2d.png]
  
\end{figure}

\lstset{language=C++,
                basicstyle=\tiny,
                emph={int,char,double,float,unsigned},
                emphstyle={\color{blue}},
                numberstyle=\color{green}\tiny,
                keywordstyle=\color{red}\bf\ttfamily,
                stringstyle=\color{red}\ttfamily,
                commentstyle=\color{green}
}

\begin{lstlisting}

for (unsigned y = 0; y < input_height; y++)
for (unsigned x = 0; x < input_width; x++)
{
    float sum = 0.0;

    for (unsigned ky = 0; ky < kernel_height; ky++)
    for (unsigned kx = 0; kx < kernel_width; kx++)
    {
      sum+= kernel[ky][kx]*input[y + ky][x + kx];
    }

    output[y + kernel_height/2][x + kernel_width/2] = sum;
}
\end{lstlisting}
\end{frame}

\begin{frame}[fragile]
{\bf activation function}

tanh, sigmoid, gaussian, {\bf RELU}, leaky RELU ...
\begin{figure}
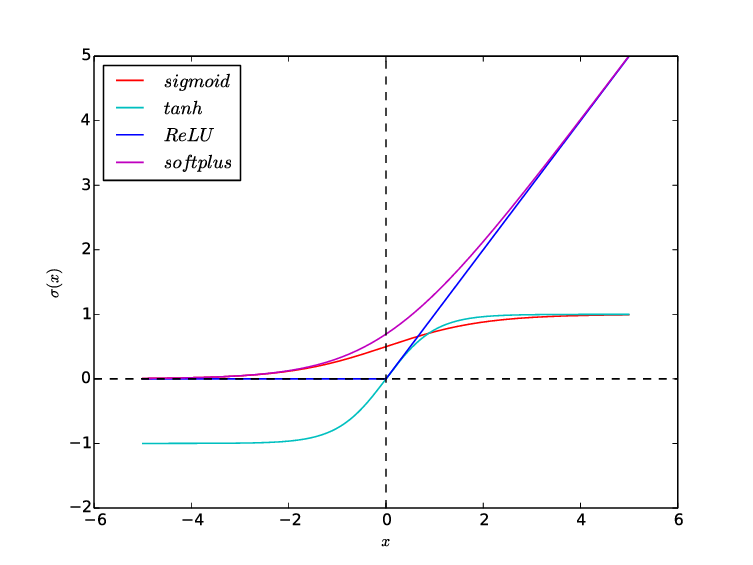
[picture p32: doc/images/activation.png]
  
\end{figure}

\begin{columns}
\begin{column}{0.5\textwidth}
\[ f(x) =
  \begin{cases}
    x       & \quad \text{if } x > 0\\
    0       & \quad \text{otherwise}
  \end{cases}
\]
\end{column}
\begin{column}{0.5\textwidth}  %%<--- here
\[ \frac{df(x)}{dx} =
  \begin{cases}
    1       & \quad \text{if } x > 0\\
    0       & \quad \text{otherwise}
  \end{cases}
\]
\end{column}
\end{columns}

\end{frame}

\begin{frame}{\bf pooling}

\begin{figure}
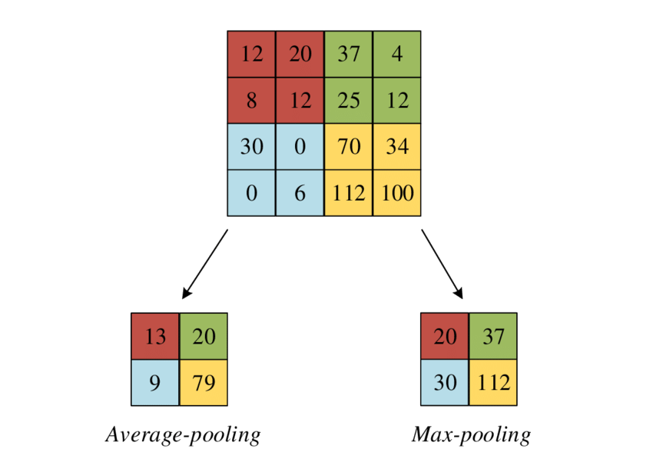
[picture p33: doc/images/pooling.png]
  
\end{figure}

\end{frame}

\begin{frame}{\bf target hardware}

\begin{table}[]
\begin{tabular}{|c|c|c|c|}
\hline
target                                                       & bits & features                                                                 & frequency                                              \\ \hline
\begin{tabular}[c]{@{}c@{}}AVR\\ Atmega 328\end{tabular}     & 8    & single cycle ADD, MUL                                                    & 20MHz                                                  \\ \hline
\begin{tabular}[c]{@{}c@{}}ARM \\ Cortex M0\end{tabular}     & 32   & single cycle ADD, MUL                                                    & 48MHz                                                  \\ \hline
\begin{tabular}[c]{@{}c@{}}ARM \\ Cortex M4, M7\end{tabular} & 32   & \begin{tabular}[c]{@{}c@{}}SIMD DUAL 16bit MAC \\ , FPU ...\end{tabular} & \begin{tabular}[c]{@{}c@{}}72MHz\\ 216MHz\end{tabular} \\ \hline
\end{tabular}
\end{table}

\end{frame}

\begin{frame}{\bf embedded network implementation}

{\bf Quantization} : convert float weights to int8\_t
\begin{align*}
  scale &= max{(|\vec{w}|_1)} \\
  \vec{w}' &= \vec{w}\frac{127}{scale}
\end{align*}

{\bf Memory saving} : use double buffer memory trick

\begin{itemize}
  \item unsigned buffer\_size = $\max_{i}$(layers[i].input\_size());
  \item buffer\_a = new int8\_t(buffer\_size);
  \item buffer\_b = new int8\_t(buffer\_size);
\end{itemize}

\begin{figure}
  
\end{figure}

\end{frame}

\begin{frame}[fragile]
{\bf optimize kernel - templates}

\lstset{language=C++,
                basicstyle=\tiny,
                emph={int,char,double,float,unsigned},
                emphstyle={\color{blue}},
                numberstyle=\color{green}\tiny,
                keywordstyle=\color{red}\bf\ttfamily,
                stringstyle=\color{red}\ttfamily,
                commentstyle=\color{green}
}

\begin{lstlisting}

templete<unsigned int kernel_size>
void convolution()
{
  for (unsigned y = 0; y < input_height; y++)
  for (unsigned x = 0; x < input_width; x++)
  {
      int sum = 0;

      for (unsigned ky = 0; ky < kernel_size; ky++)
      for (unsigned kx = 0; kx < kernel_size; kx++)
      {
        sum+= kernel[ky][kx]*input[y + ky][x + kx];
      }

      output[y + kernel_size/2][x + kernel_size/2] = (sum*scale)/127;
  }
}

...

convolution<1>(); //1x1 kernel
convolution<3>(); //3x3 kernel
convolution<5>(); //5x5 kernel
\end{lstlisting}
\end{frame}

\begin{frame}[fragile]
{\bf optimize kernel - unrolling}

\lstset{language=C++,
                basicstyle=\tiny,
                emph={int,char,double,float,unsigned},
                emphstyle={\color{blue}},
                numberstyle=\color{green}\tiny,
                keywordstyle=\color{red}\bf\ttfamily,
                stringstyle=\color{red}\ttfamily,
                commentstyle=\color{green}
}

\begin{lstlisting}

templete<unsigned int kernel_size>
void convolution()
{
  for (unsigned y = 0; y < input_height; y++)
  for (unsigned x = 0; x < input_width; x++)
  {
      int sum = 0;

      if (kernel_size == 3)
      {
        sum+= kernel[0][0]*input[y + 0][x + 0];
        sum+= kernel[0][1]*input[y + 0][x + 1];
        sum+= kernel[0][2]*input[y + 0][x + 2];

        sum+= kernel[1][0]*input[y + 1][x + 0];
        sum+= kernel[1][1]*input[y + 1][x + 1];
        sum+= kernel[1][2]*input[y + 1][x + 2];

        sum+= kernel[2][0]*input[y + 2][x + 0];
        sum+= kernel[2][1]*input[y + 2][x + 1];
        sum+= kernel[2][2]*input[y + 2][x + 2];
      }

      output[y + kernel_size/2][x + kernel_size/2] = (sum*scale)/127;
  }
}
\end{lstlisting}

\end{frame}

\begin{frame}{\bf optimize kernel - SIMD instructions}
elementary row MAC operation in 3x3 convolution : 

{ \small
  \begin{itemize}
    \item {\bf \color{green} sum}+= {\bf \color{red} kernel}[0][0]*{\bf \color{blue} input}[y + 0][x + 0];
    \item {\bf \color{green} sum}+= {\bf \color{red} kernel}[0][1]*{\bf \color{blue} input}[y + 0][x + 1];
    \item {\bf \color{green} sum}+= {\bf \color{red} kernel}[0][2]*{\bf \color{blue} input}[y + 0][x + 2];
  \end{itemize}
}

{\bf instruction : SMLADX}(int32\_t val1, int32\_t val2, int32\_t val3)
\begin{itemize}
  \item p1 = {\bf \color{red} val1}[15:0]*{\bf \color{blue} val2}[15:0]
  \item p2 = {\bf \color{red} val1}[31:16]*{\bf \color{blue} val2}[31:16]
  \item {\bf \color{green} res}[31:0] = p1 + p2 + {\bf \color{green} val3}[31:0]
\end{itemize}

\end{frame}

\begin{frame}{\bf speed up summary}

\begin{itemize}
  \item input tensor dimensions $16 \times 16 \times 16$
  \item output tensor dimensions $16 \times 16 \times 16$
\end{itemize}

\begin{table}[]
  \footnotesize
  \begin{tabular}{|l|l|l|l|}
  \hline
  \textbf{convolutional}                               & \textbf{kernel size} & \textbf{computing time {[}ms{]}} & \textbf{speed up ratio} \\ \hline
  {\color[HTML]{67FD9A} \textbf{naive}}                & 1x1                  & 109.8                            & 1.00                    \\ \hline
  {\color[HTML]{67FD9A} \textbf{naive}}                & 3x3                  & 312                              & 1.00                    \\ \hline
  {\color[HTML]{67FD9A} \textbf{naive}}                & 5x5                  & 532                              & 1.00                    \\ \hline
  {\color[HTML]{34CDF9} \textbf{template}}             & 1x1                  & 26.6                             & 4.13                    \\ \hline
  {\color[HTML]{34CDF9} \textbf{template}}             & 3x3                  & 213.6                            & 1.46                    \\ \hline
  {\color[HTML]{34CDF9} \textbf{template}}             & 5x5                  & 373.3                            & 1.43                    \\ \hline
  {\color[HTML]{FD6864} \textbf{template + unrolling}} & 1x1                  & 21                               & \textbf{5.23}           \\ \hline
  {\color[HTML]{FD6864} \textbf{template + unrolling}} & 3x3                  & 57.1                             & \textbf{5.46}           \\ \hline
  {\color[HTML]{FD6864} \textbf{template + unrolling}} & 5x5                  & 106.2                            & \textbf{5.01}           \\ \hline
  \end{tabular}
\end{table}

\end{frame}

\begin{frame}{\bf network results}

tiny architecture :
IN8x8x1 - C3x3x4 - P2x2 - C3x3x8 - P2x2 - FC5

confussion matrix :

\begin{table}[]
\begin{tabular}{|l|l|l|l|l|}
\hline
\textbf{1029}   & 12              & 0               & 0               & 0               \\ \hline
14              & \textbf{911}    & 18              & 0               & 0               \\ \hline
0               & 21              & \textbf{959}    & 6               & 0               \\ \hline
0               & 0               & 21              & \textbf{968}    & 18              \\ \hline
0               & 0               & 0               & 11              & \textbf{1012}   \\ \hline
                &                 &                 &                 &                 \\ \hline
\textbf{98.658} & \textbf{96.504} & \textbf{96.092} & \textbf{98.274} & \textbf{98.252} \\ \hline
\end{tabular}
\end{table}

success count     4879 \\
miss count         121 \\
accuracy         97.58\% \\

\end{frame}

\begin{frame}{\bf what is next?}
reinforcement learning to take full controll - \\
{\bf Advatage Actor Critic - A2C}

\begin{columns}

  \begin{column}{0.3\textwidth}

      \includemovie[
      poster,
      autoplay,
      externalviewer,
      inline=false,
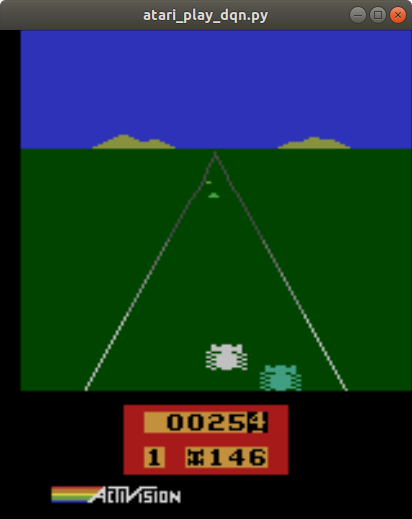
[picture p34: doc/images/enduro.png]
      text={  }
    ]{3cm}{4cm}{../video/atari_enduro.mp4}

  \end{column}

  \begin{column}{0.7\textwidth}  %%<--- here

      \begin{figure}
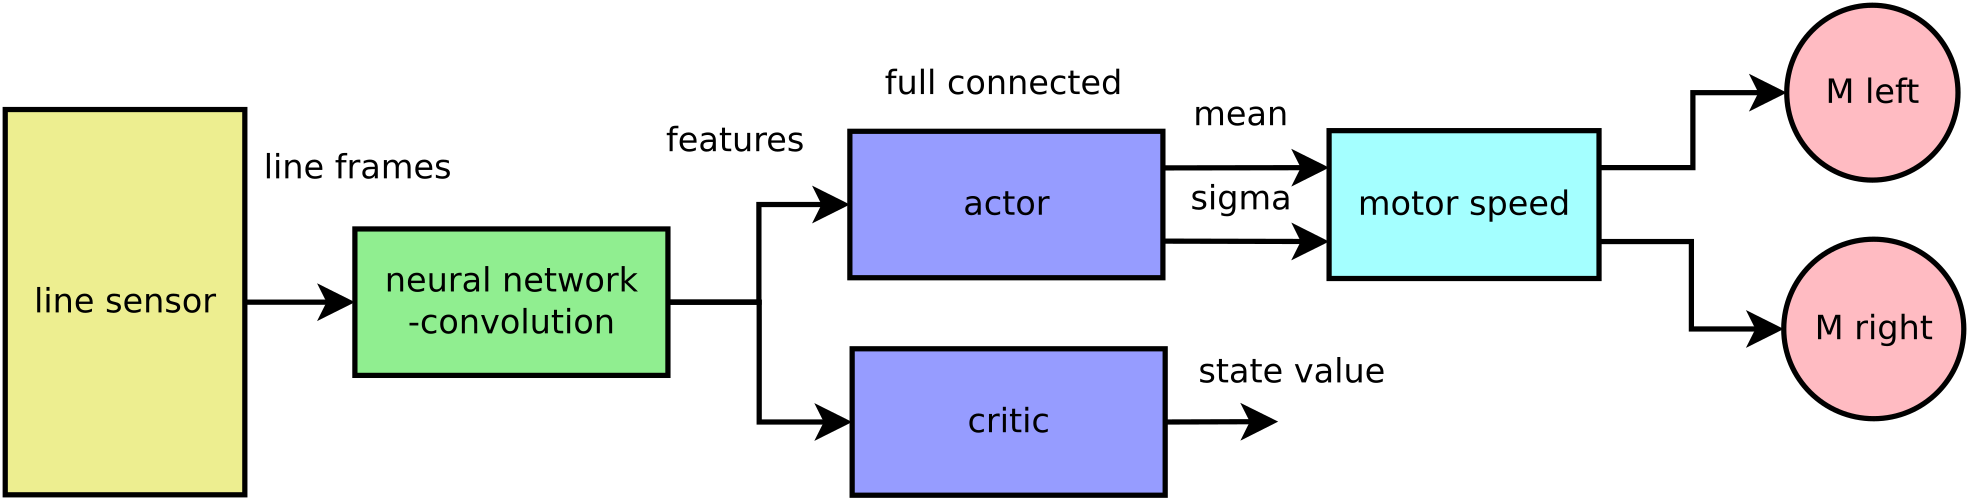
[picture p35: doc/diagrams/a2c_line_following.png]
        
      \end{figure}

  \end{column}

\end{columns}

\begin{align*}
\mathcal{L}_{actor}&= -\left( R(n) + \gamma Q(s(n+1); \phi) - Q(s(n); \phi)  \right) log \pi(s, a; \theta) \\
\mathcal{L}_{critic}&= \left( R(n) + \gamma Q(s(n+1); \phi) - Q(s(n); \phi)  \right)^2 \\
\mathcal{L}_{entropy}&= \sum_a \pi(s, a; \theta) log \pi(s, a; \theta)
\end{align*}

\end{frame}

\begin{frame}{\bf Q\&A}

\begin{figure}
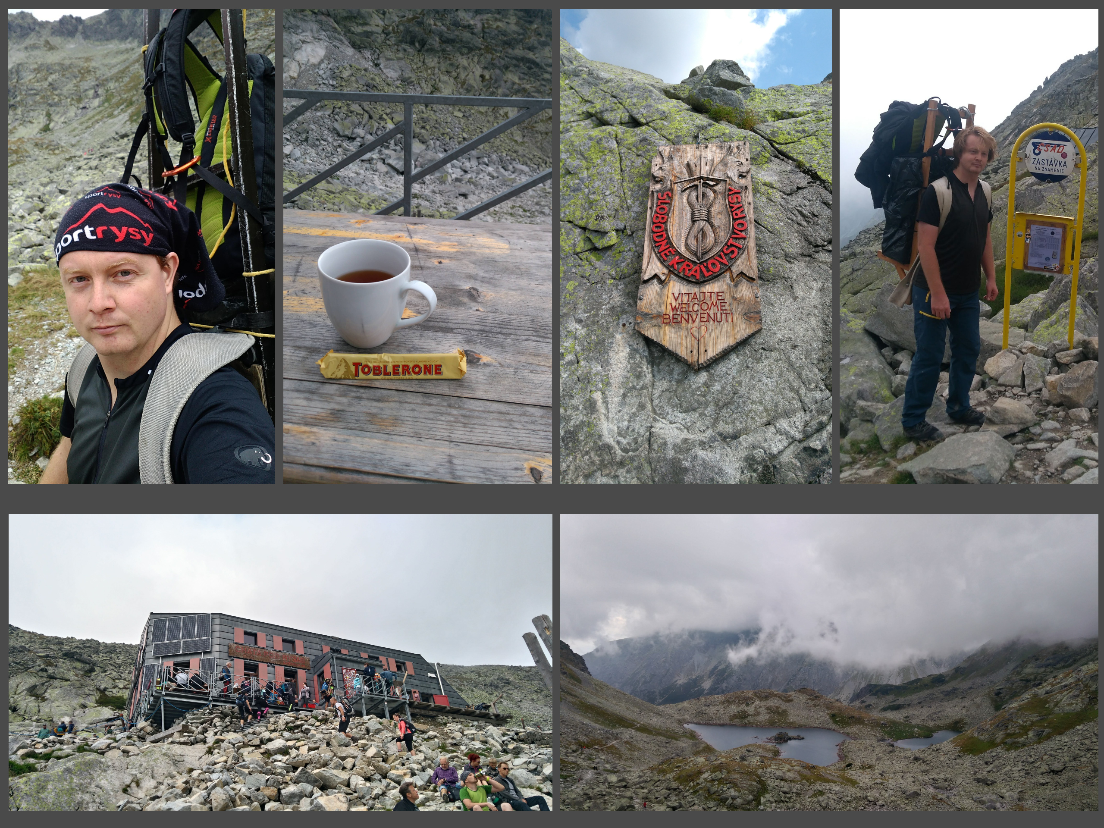
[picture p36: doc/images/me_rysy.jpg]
  
\end{figure}

\centering {
michal.nand@gmail.com, github \url{https://github.com/michalnand}
}

\end{frame}

\end{document}

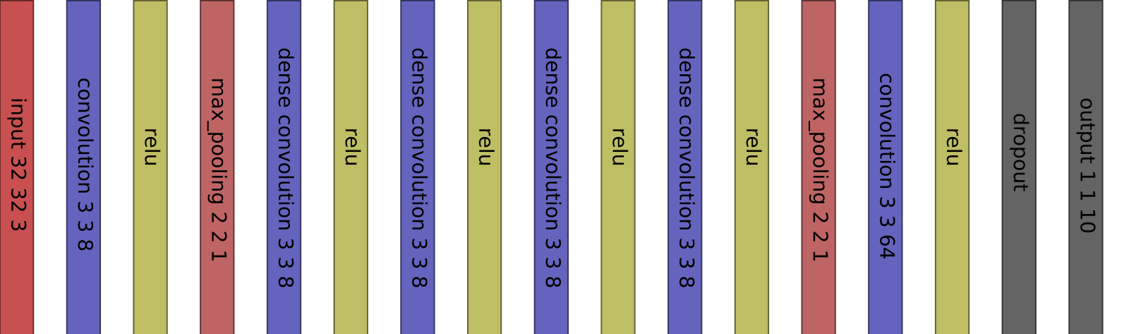
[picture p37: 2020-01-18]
doc/images/cnn_architecture_example.png

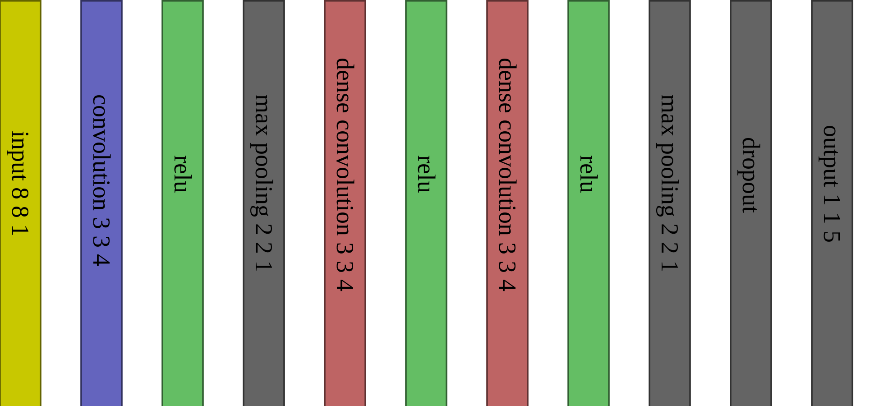
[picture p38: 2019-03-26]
doc/network/cnn_architecture.png

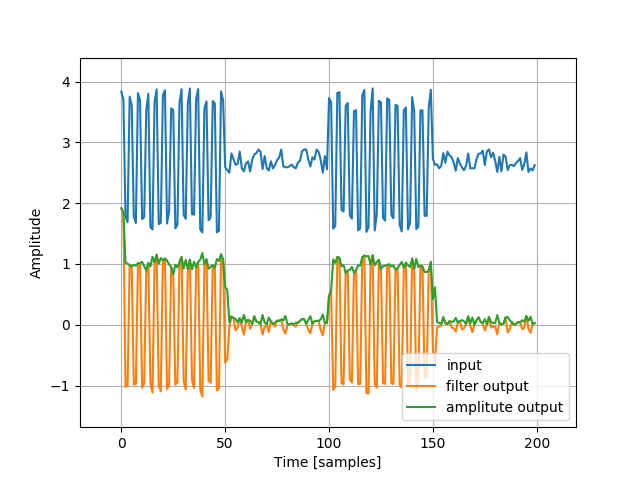
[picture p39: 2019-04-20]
src/tools/filter_design/response_r_0.0.png

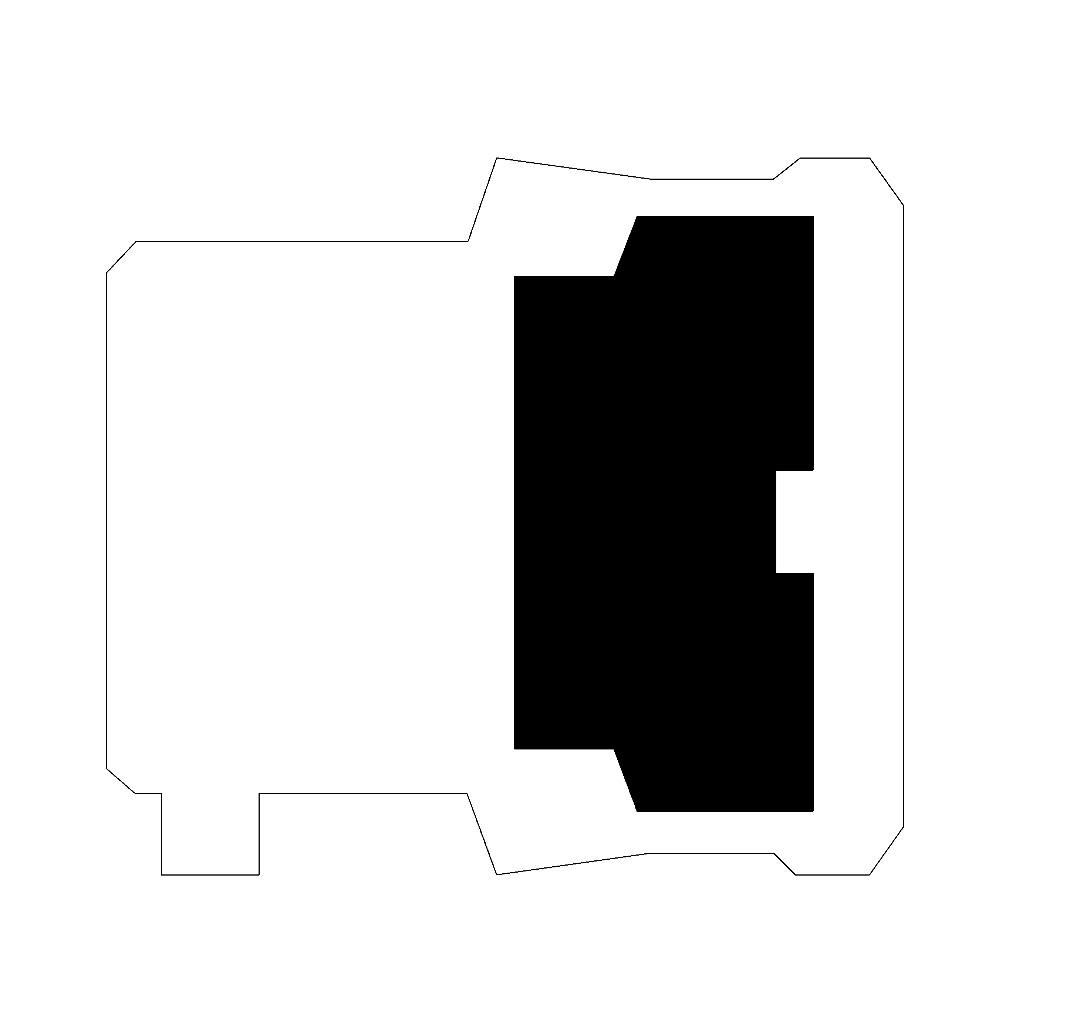
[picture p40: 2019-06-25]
hardware/outline.png

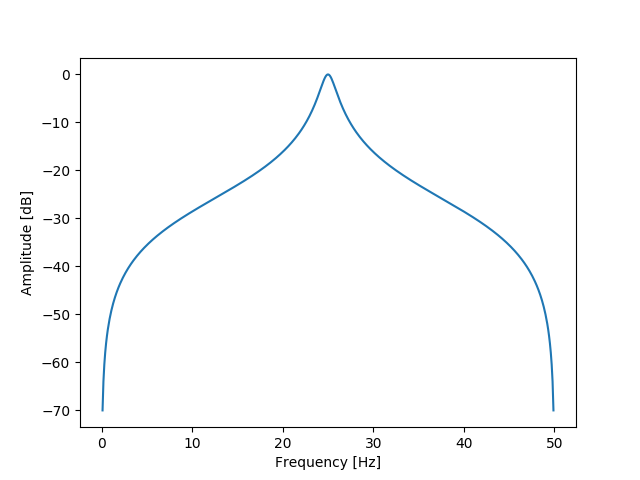
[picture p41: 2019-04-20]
src/tools/filter_design/frequency_response_r_0.95.png

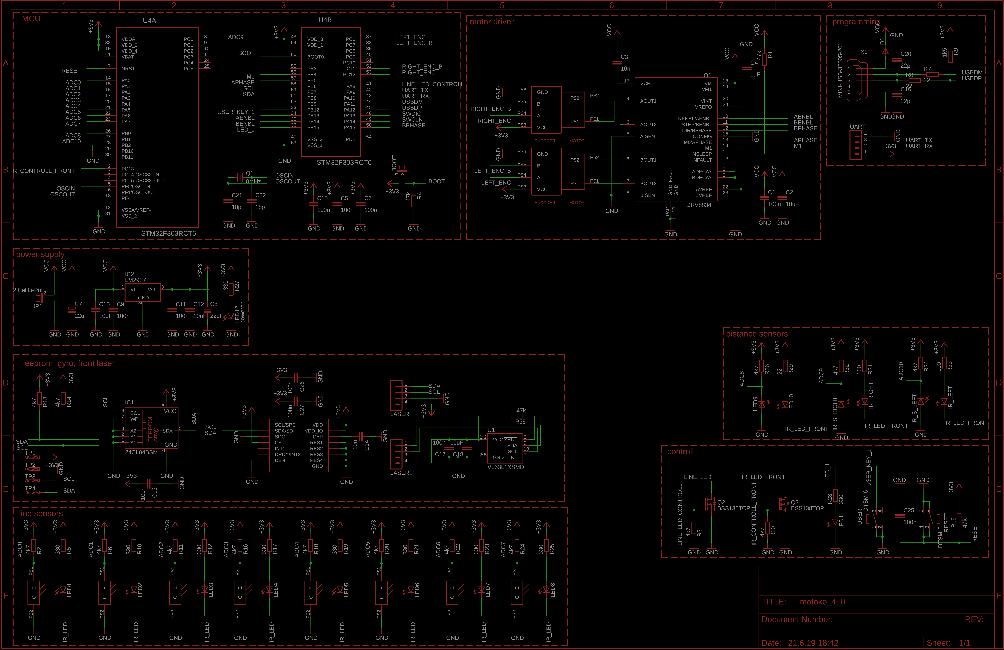
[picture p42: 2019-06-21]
hardware/schem_black.png

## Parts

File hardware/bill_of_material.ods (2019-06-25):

type | count | mouser_id | unit price | total price
STM32F303RBT7 | 3 | 511-STM32F303RBT7 | 5.19 | 15.57
DRV8834PWPR | 5 | 595-DRV8834PWPR | 2.34 | 11.7
LM2937IMP-3.3/NOPB | 5 | 926-LM2937IMP3.3NOPB | 1.54 | 7.7
24FC256T-I/SN | 5 | 579-24FC256T-I/SN | 0.681 | 3.405
LSM6DS3HTR | 5 | 511-LSM6DS3HTR | 2.54 | 12.7
VL53L1CXV0FY/1 | 5 | 511-VL53L1CXV0FY/1 | 5.62 | 28.1
BSS138 | 20 | 512-BSS138 | 0.262 | 5.24
SFH 3710-Z | 30 | 720-SFH3710-Z | 0.917 | 27.51
ABM3B-8.000MHZ-B2-T | 5 | 815-ABM3B-8.0-B2-T | 0.445 | 2.225
IR TX, OED-EL-1L1 | 12 | 696-OED-EL-1L1 | 0.611 | 7.332
IR RX, 1540051EC3590 | 12 | 710-1540051EC3590 | 0.445 | 5.34
mini USB | 5 | 710-651305142821 | 2.18 | 10.9
4k7 | 100 | 71-CRCW08054K70FKEAC | 0.02 | 2
22R | 100 | 279-CRGP0805F22R | 0.032 | 3.2
100n | 100 | 710-885012207072 | 0.06 | 6
10uF | 30 | 963-EMK212ABJ106MG-T | 0.063 | 1.89
18p | 30 | 80-C0805C180J5HACTU | 0.037 | 1.11
22uF | 30 | 647-UCQ1C220MCL1GB | 0.261 | 7.83
47uF | 30 | 647-UCQ1C470MCL1GB | 0.443 | 13.29
button | 10 | 506-2-1977223-9 | 0.21 | 2.1
 |  | total |  | 175.142

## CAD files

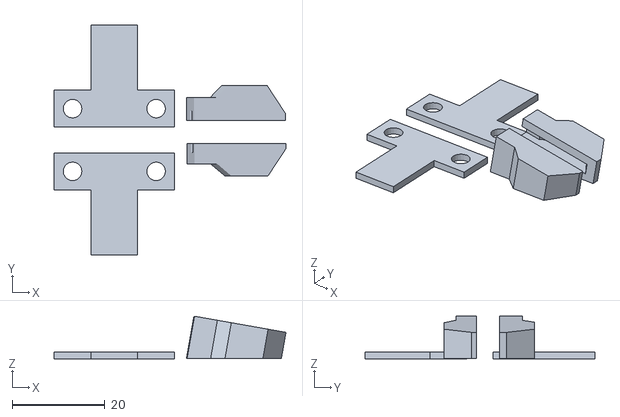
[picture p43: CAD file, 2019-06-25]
hardware/chassis/motoko_4_chassis.stl
50.0 x 49.5 x 9.15

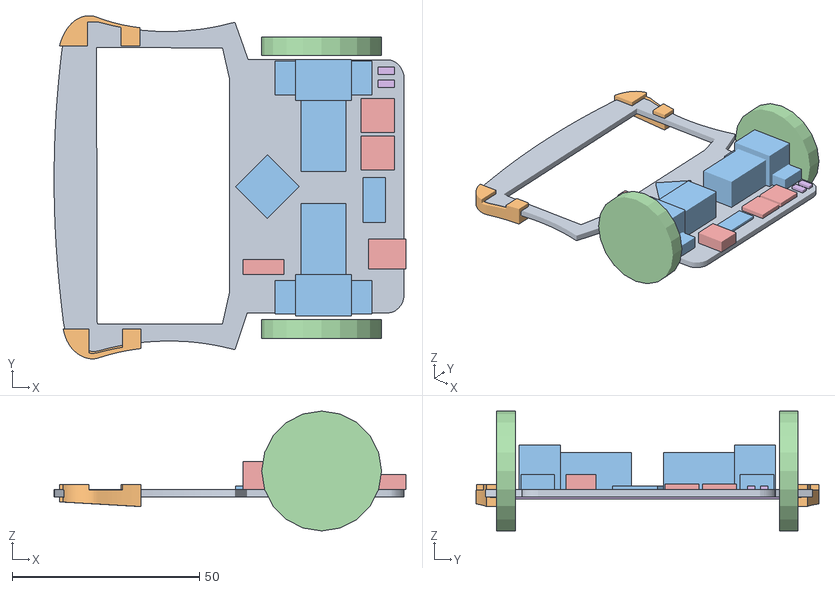
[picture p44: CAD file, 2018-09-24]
src/tools/robot_debug_py/resources/robot_model/model.obj
93.9 x 91.6 x 32.0

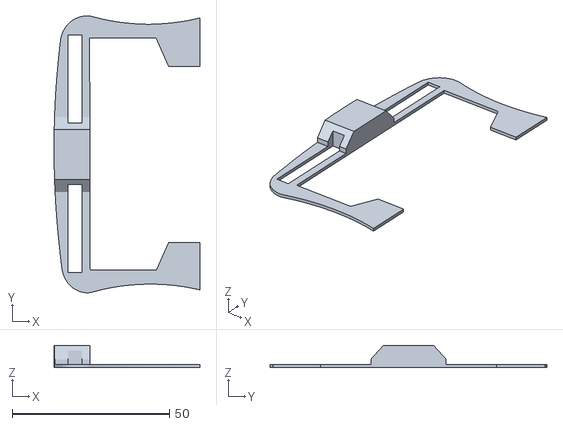
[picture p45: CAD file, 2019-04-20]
hardware/chassis/motoko_sensor_shield.stl
46.4 x 88.0 x 7.00

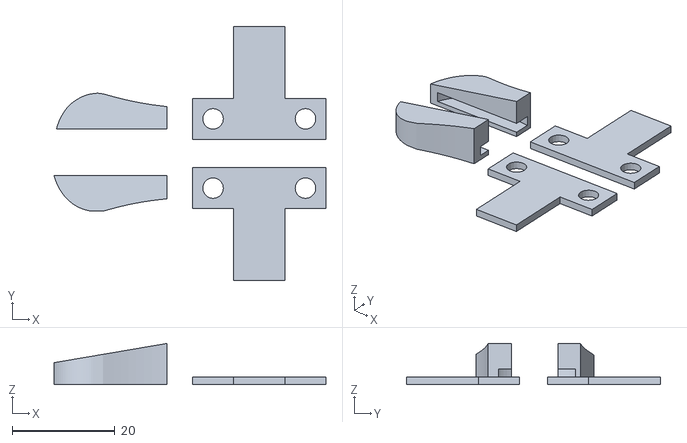
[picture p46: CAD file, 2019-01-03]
hardware/chassis/motoko_front.stl
53.0 x 49.5 x 8.00

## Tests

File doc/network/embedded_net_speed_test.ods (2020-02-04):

full connected | input size | computing time [ms] | speed up ratio
naive | 64 | 0.016 | 1.00
naive | 256 | 0.064 | 1.00
naive | 1024 | 0.252 | 1.00
unrolled | 64 | 0.01 | 1.60
unrolled | 256 | 0.037 | 1.73
unrolled | 1024 | 0.147 | 1.71
convolutional | input size | kernels count | kernel size | computing time [ms] | speed up ratio
naive | 16x16x16 | 16 | 1x1 | 109.8 | 1.00
naive | 16x16x16 | 16 | 3x3 | 312 | 1.00
naive | 16x16x16 | 16 | 5x5 | 532 | 1.00
template | 16x16x16 | 16 | 1x1 | 26.6 | 4.13
template | 16x16x16 | 16 | 3x3 | 213.6 | 1.46
template | 16x16x16 | 16 | 5x5 | 373.3 | 1.43
template + unrolling | 16x16x16 | 16 | 1x1 | 21 | 5.23
template + unrolling | 16x16x16 | 16 | 3x3 | 57.1 | 5.46
template + unrolling | 16x16x16 | 16 | 5x5 | 106.2 | 5.01
convolutional | kernel size | computing time [ms] | speed up ratio
naive | 1x1 | 109.8 | 1.00
naive | 3x3 | 312 | 1.00
naive | 5x5 | 532 | 1.00
template | 1x1 | 26.6 | 4.13
template | 3x3 | 213.6 | 1.46
template | 5x5 | 373.3 | 1.43
template + unrolling | 1x1 | 21 | 5.23
template + unrolling | 3x3 | 57.1 | 5.46
template + unrolling | 5x5 | 106.2 | 5.01

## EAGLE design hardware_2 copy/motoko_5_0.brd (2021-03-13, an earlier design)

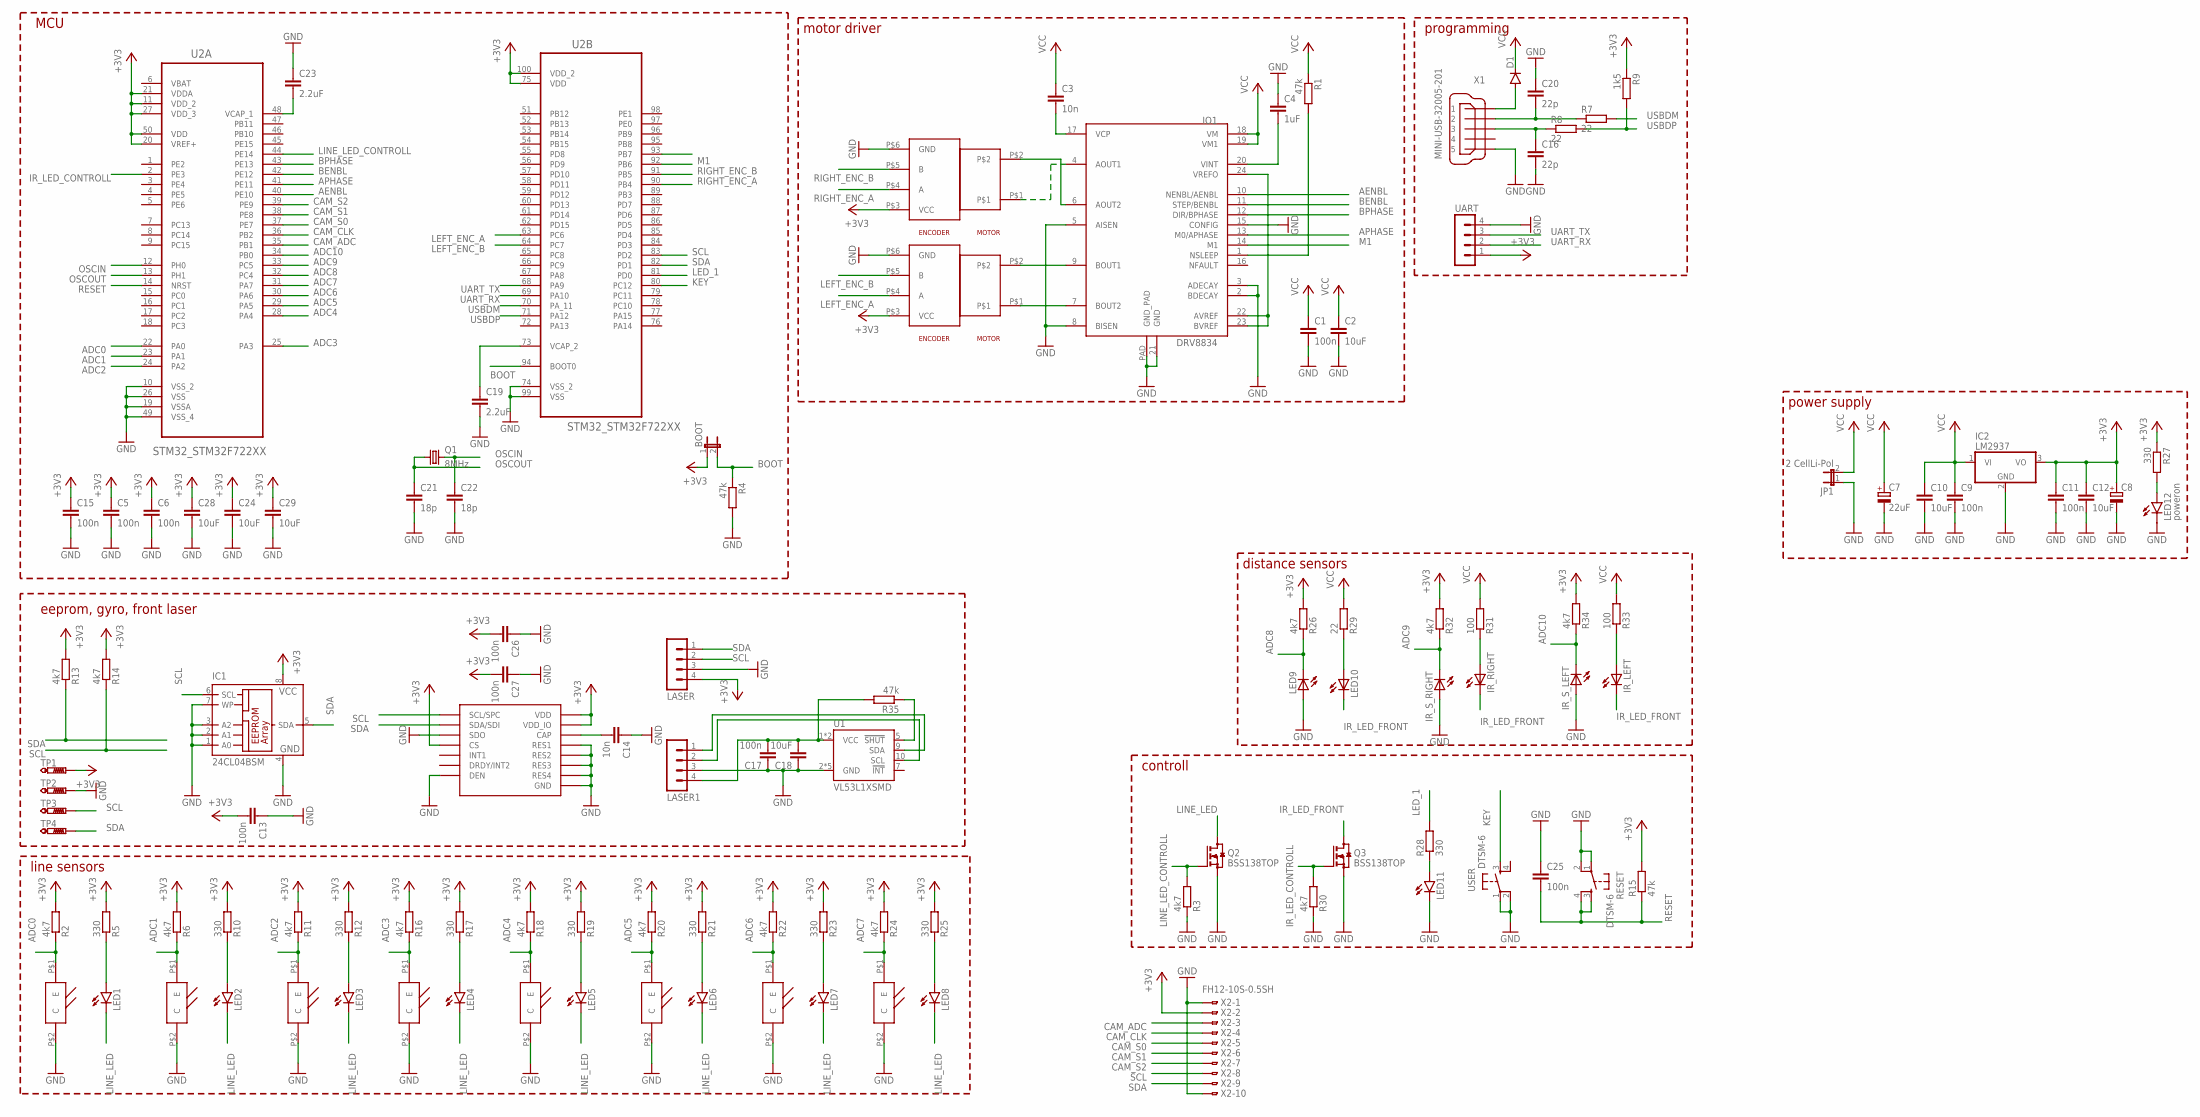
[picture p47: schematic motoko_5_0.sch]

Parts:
BOOT: JP1E; JP1
C1: 100n; C1206
C2: 10uF; C1206
C3: 10n; C1206
C4: 1uF; C1206
C5, C6, C9, C11, C13, C15, C17, C25, C26, C27: 100n; C0805
C7: 22uF; 153CLV-0505
C8: CPOL-EU140CLH-1010; 140CLH-1010
C10, C12, C18, C24, C28, C29: 10uF; C0805
C14: 10n; C0805
C16, C20: 22p; C0805
C19, C23: 2.2uF; C0805
C21, C22: 18p; C0805
D1: DIODE-SMB; SMB
IC1: 24CL04BSM; SO-08M
IC2: LM2937; TO263-3
IO1: DRV8834; DRV8834_PCK
IR_LEFT: LED5MM
IR_RIGHT: LED5MM
IR_S_LEFT: LED5MM
IR_S_RIGHT: LED5MM
JP1: 2 CellLi-Pol; JP1
LASER, LASER1: MA04-1
LED1, LED2, LED3, LED4, LED5, LED6, LED7, LED8, LED11: LEDCHIPLED_1206; CHIPLED_1206
LED9, LED10: LED5MM
LED12: poweron; CHIPLED_1206
LSM6DS0: ST_L3GD20H; ST_LGA16L
Q1: 8MHz; CTS406
Q2, Q3: BSS138TOP; SOT23
R1: 47k; M1206
R2, R3, R6, R11, R13, R14, R16, R18, R20, R22, R24, R26, R30, R32, R34: 4k7; M0805
R4, R15, R35: 47k; M0805
R5, R10, R12, R17, R19, R21, R23, R25, R27, R28: 330; M0805
R7, R8, R29: 22; M0805
R9: 1k5; M0805
R31, R33: 100; M0805
RESET: DTSM-6
TP1, TP2, TP3, TP4: PTR1B1,27; B1,27
U1: VL53L1XSMD; VL53L1X
U2: STM32_STM32F722XX; STM32_QFP50P1600X1600X160-100N
U$3, U$4, U$5, U$6, U$7, U$8, U$9, U$10: SFH3710
U$11, U$12: POLOLU_GEAR_MOTORPOLO; POLOLU_GEAR_MOTOR
UART: MA04-1
USER: DTSM-6
X1: MINI-USB-32005-201; 32005-201
X2: FH12-10S-0.5SH

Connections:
+3V3: BOOT.1, C5.1, C6.1, C8.+, C11.1, C12.1, C13.2, C15.1, C24.1, C26.2, C27.2, C28.1, C29.1, IC1.8 (VCC), IC2.3 (VO), LASER.4, LSM6DS0.P$1 (VDD_IO), LSM6DS0.P$5 (CS), LSM6DS0.P$16 (VDD), R2.2, R5.2, R6.2, R9.1, R10.2, R11.2, R12.2, R13.2, R14.2, R15.2, R16.2, R17.2, R18.2, R19.2, R20.2, R21.2, R22.2, R23.2, R24.2, R25.2, R26.2, R27.1, R32.2, R34.2, TP1.TP, U2.11 (VDD_2), U2.20 (VREF+), U2.21 (VDDA), U2.27 (VDD_3), U2.50 (VDD), U2.75 (VDD), U2.100 (VDD_2), U$11.P$3 (VCC), U$12.P$3 (VCC), UART.1, X2.2
ADC0: R2.1, U2.22 (PA0), U$3.P$1 (E)
ADC1: R6.1, U2.23 (PA1), U$4.P$1 (E)
ADC2: R11.1, U2.24 (PA2), U$5.P$1 (E)
ADC3: R16.1, U2.25 (PA3), U$6.P$1 (E)
ADC4: R18.1, U2.28 (PA4), U$7.P$1 (E)
ADC5: R20.1, U2.29 (PA5), U$8.P$1 (E)
ADC6: R22.1, U2.30 (PA6), U$9.P$1 (E)
ADC7: R24.1, U2.31 (PA7), U$10.P$1 (E)
ADC8: LED9.K (C), R26.1, U2.32 (PC4)
ADC9: IR_S_RIGHT.K (C), R32.1, U2.33 (PC5)
ADC10: IR_S_LEFT.K (C), R34.1, U2.34 (PB0)
AENBL: IO1.10 (NENBL/AENBL), U2.40 (PE10)
APHASE: IO1.13 (M0/APHASE), U2.41 (PE11)
BENBL: IO1.11 (STEP/BENBL), U2.42 (PE12)
BOOT: BOOT.2, R4.1, U2.94 (BOOT0)
BPHASE: IO1.12 (DIR/BPHASE), U2.43 (PE13)
CAM_ADC: U2.35 (PB1), X2.3
CAM_CLK: U2.36 (PB2), X2.4
CAM_S0: U2.37 (PE7), X2.5
CAM_S1: U2.38 (PE8), X2.6
CAM_S2: U2.39 (PE9), X2.7
GND: C1.2, C2.2, C4.1, C5.2, C6.2, C7.-, C8.-, C9.2, C10.2, C11.2, C12.2, C13.1, C14.1, C15.2, C16.2, C17.1, C18.1, C19.2, C20.1, C21.2, C22.2, C23.1, C24.2, C25.1, C26.1, C27.1, C28.2, C29.2, IC1.1 (A0), IC1.2 (A1), IC1.3 (A2), IC1.4 (GND), IC1.7 (WP), IC2.2 (GND), IO1.2 (BDECAY), IO1.3 (ADECAY), IO1.5 (AISEN), IO1.8 (BISEN), IO1.15 (CONFIG), IO1.21 (GND), IO1.PAD (GND_PAD), IR_S_LEFT.A, IR_S_RIGHT.A, JP1.1, LASER.3, LASER1.3, LED9.A, LED11.C, LED12.C, LSM6DS0.P$4 (SDO), LSM6DS0.P$8 (DEN), LSM6DS0.P$9 (RES1), LSM6DS0.P$10 (RES2), LSM6DS0.P$11 (RES3), LSM6DS0.P$12 (GND), LSM6DS0.P$13 (GND), LSM6DS0.P$15 (RES4), Q2.2 (S), Q3.2 (S), R3.1, R4.2, R30.1, RESET.1, RESET.2, TP2.TP, U1.2 (GND), U1.3 (GND), U1.4 (GND), U1.6 (GND), U1.12 (GND), U2.10 (VSS_2), U2.19 (VSSA), U2.26 (VSS), U2.49 (VSS_4), U2.74 (VSS_2), U2.99 (VSS), U$3.P$2 (C), U$4.P$2 (C), U$5.P$2 (C), U$6.P$2 (C), U$7.P$2 (C), U$8.P$2 (C), U$9.P$2 (C), U$10.P$2 (C), U$11.P$6 (GND), U$12.P$6 (GND), UART.4, USER.1, USER.2, X1.5, X2.1, X2.10
IR_LED_CONTROLL: Q3.1 (G), R30.2, U2.2 (PE3)
IR_LED_FRONT: IR_LEFT.K (C), IR_RIGHT.K (C), LED10.K (C), Q3.3 (D)
KEY: U2.80 (PC12), USER.3
LED_1: R28.2, U2.81 (PD0)
LEFT_ENC_A: U2.63 (PC6), U$11.P$4 (A)
LEFT_ENC_B: U2.64 (PC7), U$11.P$5 (B)
LINE_LED: LED1.C, LED2.C, LED3.C, LED4.C, LED5.C, LED6.C, LED7.C, LED8.C, Q2.3 (D)
LINE_LED_CONTROLL: Q2.1 (G), R3.2, U2.44 (PE14)
M1: IO1.14 (M1), U2.92 (PB6)
unnamed: IO1.6 (AOUT2), U$12.P$2
unnamed: IO1.4 (AOUT1), U$12.P$1
unnamed: IO1.7 (BOUT2), U$11.P$1
unnamed: IO1.9 (BOUT1), U$11.P$2
unnamed: C3.2, IO1.17 (VCP)
unnamed: C14.2, LSM6DS0.P$14 (CAP)
unnamed: LED10.A, R29.1
unnamed: IO1.22 (AVREF), IO1.23 (BVREF), IO1.24 (VREFO)
unnamed: IO1.1 (NSLEEP), R1.2
unnamed: IR_LEFT.A, R33.1
unnamed: LED1.A, R5.1
unnamed: LED2.A, R10.1
unnamed: LED3.A, R12.1
unnamed: LED4.A, R17.1
unnamed: LED5.A, R19.1
unnamed: LED6.A, R21.1
unnamed: LED7.A, R23.1
unnamed: LED8.A, R25.1
unnamed: C4.2, IO1.20 (VINT)
unnamed: LED12.A, R27.2
unnamed: IR_RIGHT.A, R31.1
unnamed: C19.1, U2.73 (VCAP_2)
unnamed: C17.2, C18.2, LASER1.4, R35.2, U1.1 (VCC), U1.11 (VCC)
unnamed: LASER1.1, U1.9 (SDA)
unnamed: LASER1.2, U1.10 (SCL)
unnamed: R35.1, U1.5 (!SHUT)
unnamed: C23.2, U2.48 (VCAP_1)
unnamed: LED11.A, R28.1
unnamed: C20.2, R7.1, X1.2
unnamed: C16.1, R8.1, X1.3
unnamed: D1.A, X1.1
OSCIN: C22.1, Q1.3 (2), U2.12 (PH0)
OSCOUT: C21.1, Q1.1, U2.13 (PH1)
RESET: C25.2, R15.1, RESET.3, RESET.4, U2.14 (NRST)
RIGHT_ENC_A: U2.90 (PB4), U$12.P$4 (A)
RIGHT_ENC_B: U2.91 (PB5), U$12.P$5 (B)
SCL: IC1.6 (SCL), LASER.2, LSM6DS0.P$2 (SCL/SPC), R14.1, TP3.TP, U2.83 (PD2), X2.8
SDA: IC1.5 (SDA), LASER.1, LSM6DS0.P$3 (SDA/SDI), R13.1, TP4.TP, U2.82 (PD1), X2.9
UART_RX: U2.69 (PA10), UART.2
UART_TX: U2.68 (PA9), UART.3
USBDM: R7.2, U2.70 (PA_11)
USBDP: R8.2, R9.2, U2.71 (PA12)
VBAT: U2.6 (VBAT)
VCC: C1.1, C2.1, C3.1, C7.+, C9.1, C10.1, D1.C, IC2.1 (VI), IO1.18 (VM), IO1.19 (VM1), JP1.2, R1.1, R29.2, R31.2, R33.2

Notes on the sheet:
power supply
line sensors
programming
MCU
motor driver
distance sensors
controll
eeprom, gyro, front laser

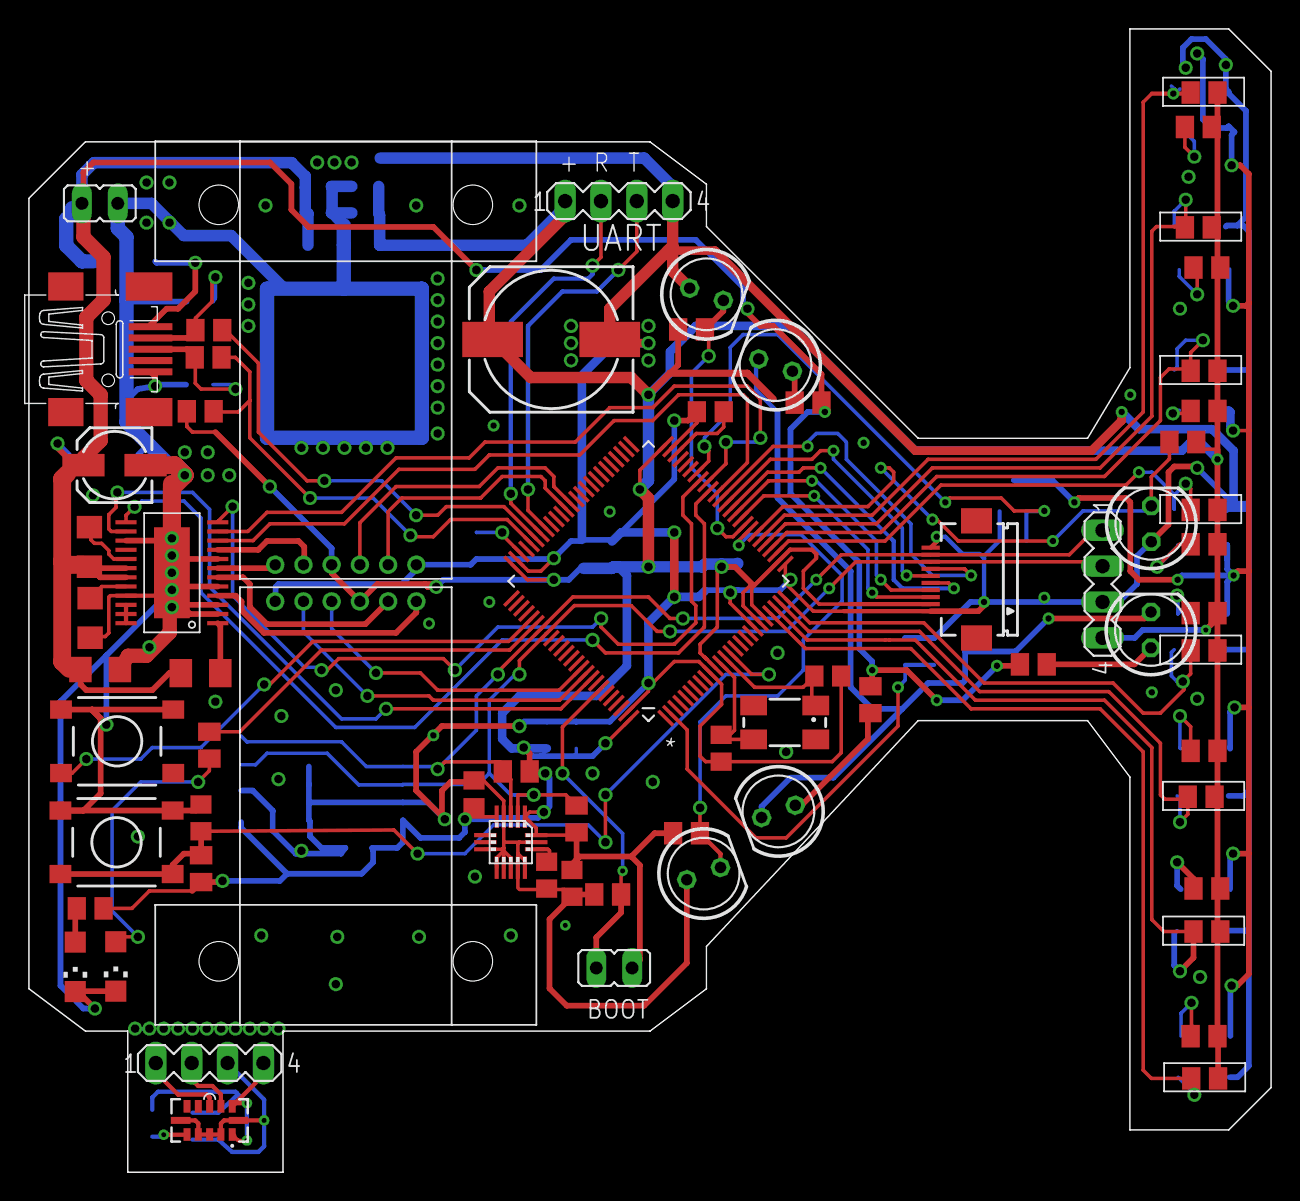
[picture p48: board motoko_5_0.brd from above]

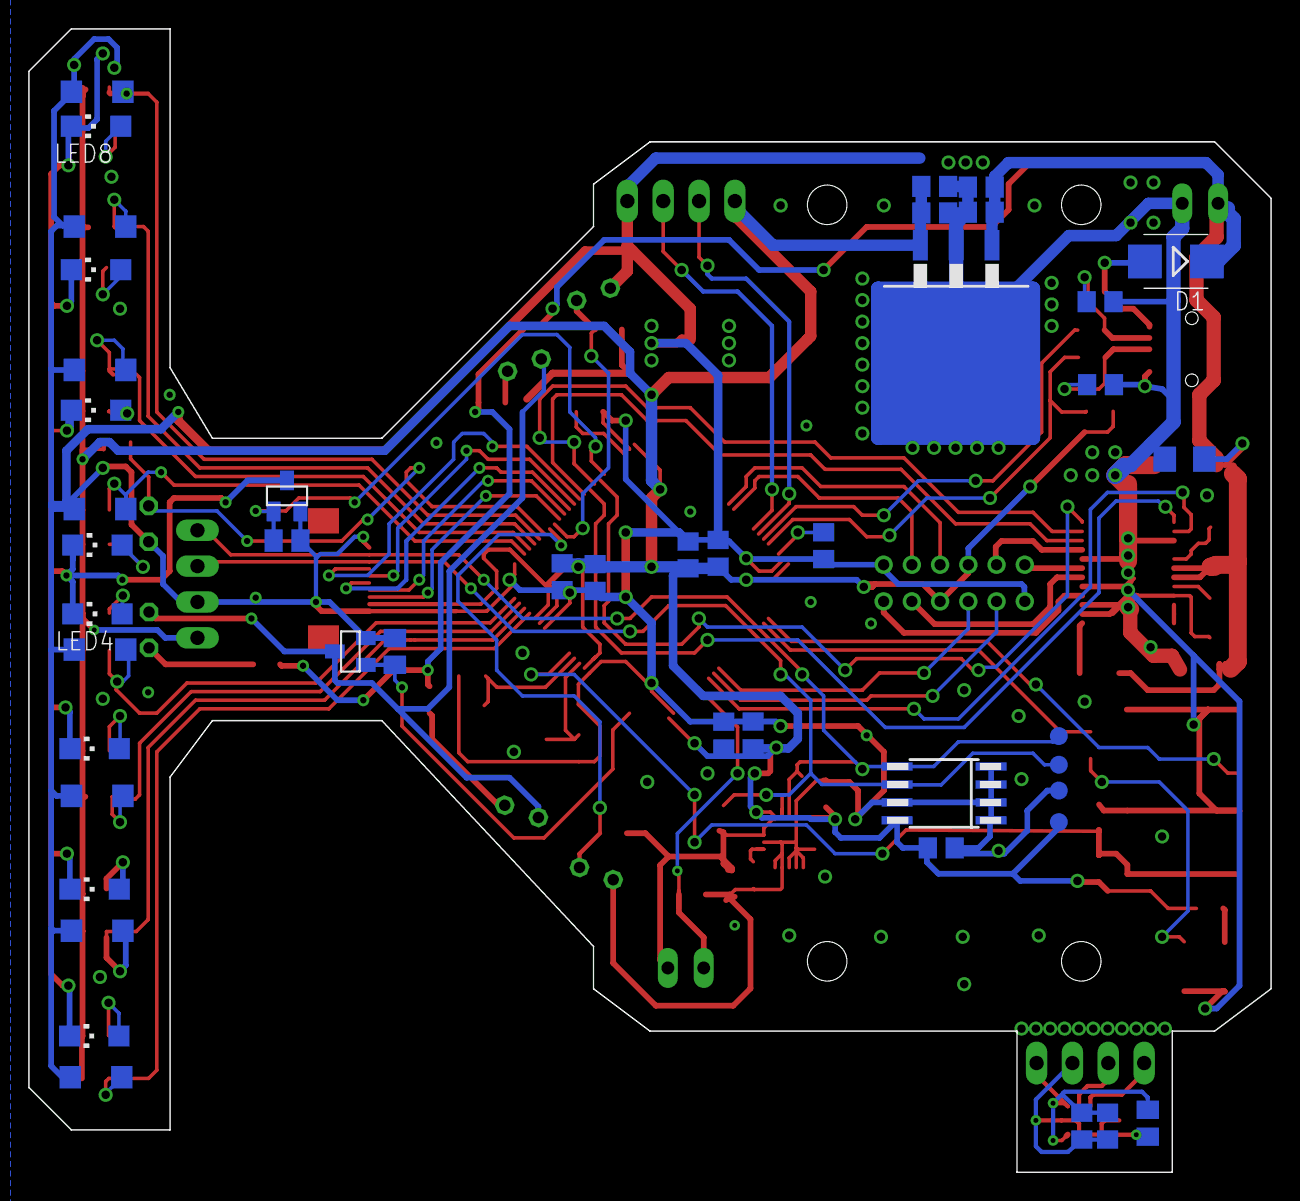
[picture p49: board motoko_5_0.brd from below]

Board: 2 copper layers, 88.0 x 81.0 mm, 113 parts (45 on the bottom side), 75 nets.

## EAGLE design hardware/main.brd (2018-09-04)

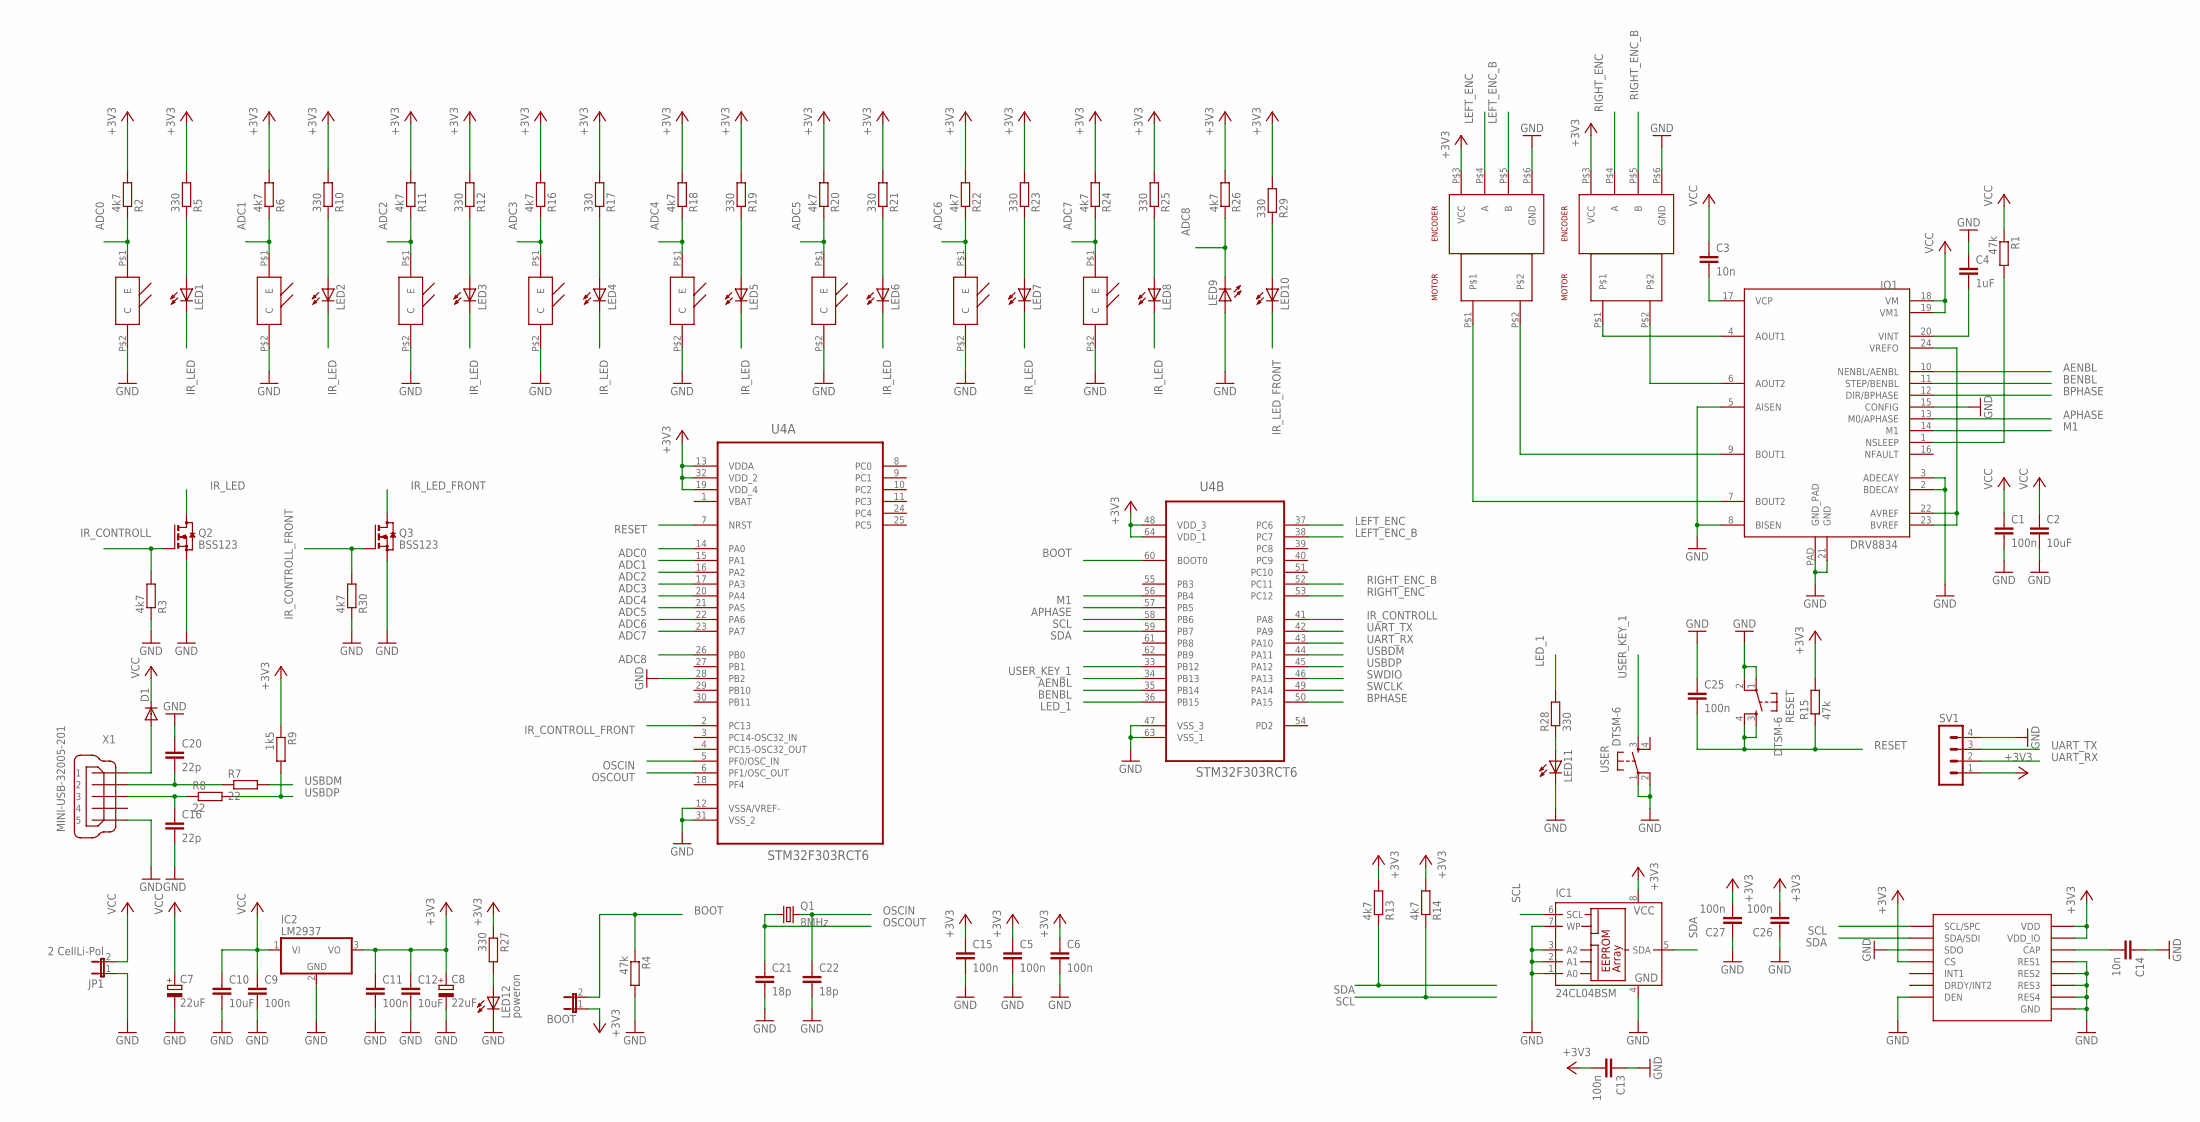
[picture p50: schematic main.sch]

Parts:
BOOT: JP1E; JP1
C1: 100n; C1206
C2: 10uF; C1206
C3: 10n; C1206
C4: 1uF; C1206
C5, C6, C9, C11, C13, C15, C25, C26, C27: 100n; C0805
C7, C8: 22uF; 153CLV-0505
C10, C12: 10uF; C0805
C14: 10n; C0805
C16, C20: 22p; C0805
C21, C22: 18p; C0805
D1: DIODE-SMB; SMB
IC1: 24CL04BSM; SO-08M
IC2: LM2937; TO263-3
IO1: DRV8834; DRV8834_PCK
JP1: 2 CellLi-Pol; JP1
LED1, LED2, LED3, LED4, LED5, LED6, LED7, LED8, LED11: LEDCHIPLED_1206; CHIPLED_1206
LED9, LED10: LED5MM
LED12: poweron; CHIPLED_1206
LSM6DS0: L3GD20H; LGA16L
Q1: 8MHz; CTS406
Q2, Q3: BSS123; SOT23
R1: 47k; M1206
R2, R3, R6, R11, R13, R14, R16, R18, R20, R22, R24, R26, R30: 4k7; M0805
R4, R15: 47k; M0805
R5, R10, R12, R17, R19, R21, R23, R25, R27, R28, R29: 330; M0805
R7, R8: 22; M0805
R9: 1k5; M0805
RESET: DTSM-6
SV1: MA04-1
U4: STM32F303RCT6; QFP50P1200X1200X160-64N
U$3, U$4, U$5, U$6, U$7, U$8, U$9, U$10: SFH3710
U$11, U$12: POLOLU_GEAR_MOTORPOLO; POLOLU_GEAR_MOTOR
USER: DTSM-6
X1: MINI-USB-32005-201; 32005-201

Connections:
+3V3: BOOT.1, C5.1, C6.1, C8.+, C11.1, C12.1, C13.2, C15.1, C26.2, C27.2, IC1.8 (VCC), IC2.3 (VO), LSM6DS0.P$1 (VDD_IO), LSM6DS0.P$5 (CS), LSM6DS0.P$16 (VDD), R2.2, R5.2, R6.2, R9.1, R10.2, R11.2, R12.2, R13.2, R14.2, R15.2, R16.2, R17.2, R18.2, R19.2, R20.2, R21.2, R22.2, R23.2, R24.2, R25.2, R26.2, R27.1, R29.2, SV1.1, U4.13 (VDDA), U4.19 (VDD_4), U4.32 (VDD_2), U4.48 (VDD_3), U4.64 (VDD_1), U$11.P$3 (VCC), U$12.P$3 (VCC)
ADC0: R2.1, U4.14 (PA0), U$3.P$1 (E)
ADC1: R6.1, U4.15 (PA1), U$4.P$1 (E)
ADC2: R11.1, U4.16 (PA2), U$5.P$1 (E)
ADC3: R16.1, U4.17 (PA3), U$6.P$1 (E)
ADC4: R18.1, U4.20 (PA4), U$7.P$1 (E)
ADC5: R20.1, U4.21 (PA5), U$8.P$1 (E)
ADC6: R22.1, U4.22 (PA6), U$9.P$1 (E)
ADC7: R24.1, U4.23 (PA7), U$10.P$1 (E)
ADC8: LED9.K (C), R26.1, U4.26 (PB0)
AENBL: IO1.10 (NENBL/AENBL), U4.34 (PB13)
APHASE: IO1.13 (M0/APHASE), U4.57 (PB5)
BENBL: IO1.11 (STEP/BENBL), U4.35 (PB14)
BOOT: BOOT.2, R4.1, U4.60 (BOOT0)
BPHASE: IO1.12 (DIR/BPHASE), U4.50 (PA15)
GND: C1.2, C2.2, C4.1, C5.2, C6.2, C7.-, C8.-, C9.2, C10.2, C11.2, C12.2, C13.1, C14.1, C15.2, C16.2, C20.1, C21.2, C22.2, C25.1, C26.1, C27.1, IC1.1 (A0), IC1.2 (A1), IC1.3 (A2), IC1.4 (GND), IC1.7 (WP), IC2.2 (GND), IO1.2 (BDECAY), IO1.3 (ADECAY), IO1.5 (AISEN), IO1.8 (BISEN), IO1.15 (CONFIG), IO1.21 (GND), IO1.PAD (GND_PAD), JP1.1, LED9.A, LED11.C, LED12.C, LSM6DS0.P$4 (SDO), LSM6DS0.P$8 (DEN), LSM6DS0.P$9 (RES1), LSM6DS0.P$10 (RES2), LSM6DS0.P$11 (RES3), LSM6DS0.P$12 (GND), LSM6DS0.P$13 (GND), LSM6DS0.P$15 (RES4), Q2.2 (S), Q3.2 (S), R3.1, R4.2, R30.1, RESET.1, RESET.2, SV1.4, U4.12 (VSSA/VREF-), U4.28 (PB2), U4.31 (VSS_2), U4.47 (VSS_3), U4.63 (VSS_1), U$3.P$2 (C), U$4.P$2 (C), U$5.P$2 (C), U$6.P$2 (C), U$7.P$2 (C), U$8.P$2 (C), U$9.P$2 (C), U$10.P$2 (C), U$11.P$6 (GND), U$12.P$6 (GND), USER.1, USER.2, X1.5
IR_CONTROLL: Q2.1 (G), R3.2, U4.41 (PA8)
IR_CONTROLL_FRONT: Q3.1 (G), R30.2, U4.2 (PC13)
IR_LED: LED1.C, LED2.C, LED3.C, LED4.C, LED5.C, LED6.C, LED7.C, LED8.C, Q2.3 (D)
IR_LED_FRONT: LED10.K (C), Q3.3 (D)
LED_1: R28.2, U4.36 (PB15)
LEFT_ENC: U4.37 (PC6), U$11.P$4 (A)
LEFT_ENC_B: U4.38 (PC7), U$11.P$5 (B)
M1: IO1.14 (M1), U4.56 (PB4)
unnamed: IO1.6 (AOUT2), U$12.P$2
unnamed: IO1.4 (AOUT1), U$12.P$1
unnamed: IO1.7 (BOUT2), U$11.P$1
unnamed: IO1.9 (BOUT1), U$11.P$2
unnamed: C3.2, IO1.17 (VCP)
unnamed: C14.2, LSM6DS0.P$14 (CAP)
unnamed: LED10.A, R29.1
unnamed: IO1.22 (AVREF), IO1.23 (BVREF), IO1.24 (VREFO)
unnamed: IO1.1 (NSLEEP), R1.2
unnamed: LED1.A, R5.1
unnamed: LED2.A, R10.1
unnamed: LED3.A, R12.1
unnamed: LED4.A, R17.1
unnamed: LED5.A, R19.1
unnamed: LED6.A, R21.1
unnamed: LED7.A, R23.1
unnamed: LED8.A, R25.1
unnamed: C4.2, IO1.20 (VINT)
unnamed: LED12.A, R27.2
unnamed: LED11.A, R28.1
unnamed: C20.2, R7.1, X1.2
unnamed: C16.1, R8.1, X1.3
unnamed: D1.A, X1.1
OSCIN: C22.1, Q1.3 (2), U4.5 (PF0/OSC_IN)
OSCOUT: C21.1, Q1.1, U4.6 (PF1/OSC_OUT)
RESET: C25.2, R15.1, RESET.3, RESET.4, U4.7 (NRST)
RIGHT_ENC: U4.53 (PC12), U$12.P$4 (A)
RIGHT_ENC_B: U4.52 (PC11), U$12.P$5 (B)
SCL: IC1.6 (SCL), LSM6DS0.P$2 (SCL/SPC), R14.1, U4.58 (PB6)
SDA: IC1.5 (SDA), LSM6DS0.P$3 (SDA/SDI), R13.1, U4.59 (PB7)
SWCLK: U4.49 (PA14)
SWDIO: U4.46 (PA13)
UART_RX: SV1.2, U4.43 (PA10)
UART_TX: SV1.3, U4.42 (PA9)
USBDM: R7.2, U4.44 (PA11)
USBDP: R8.2, R9.2, U4.45 (PA12)
USER_KEY_1: U4.33 (PB12), USER.3
VBAT: U4.1 (VBAT)
VCC: C1.1, C2.1, C3.1, C7.+, C9.1, C10.1, D1.C, IC2.1 (VI), IO1.18 (VM), IO1.19 (VM1), JP1.2, R1.1

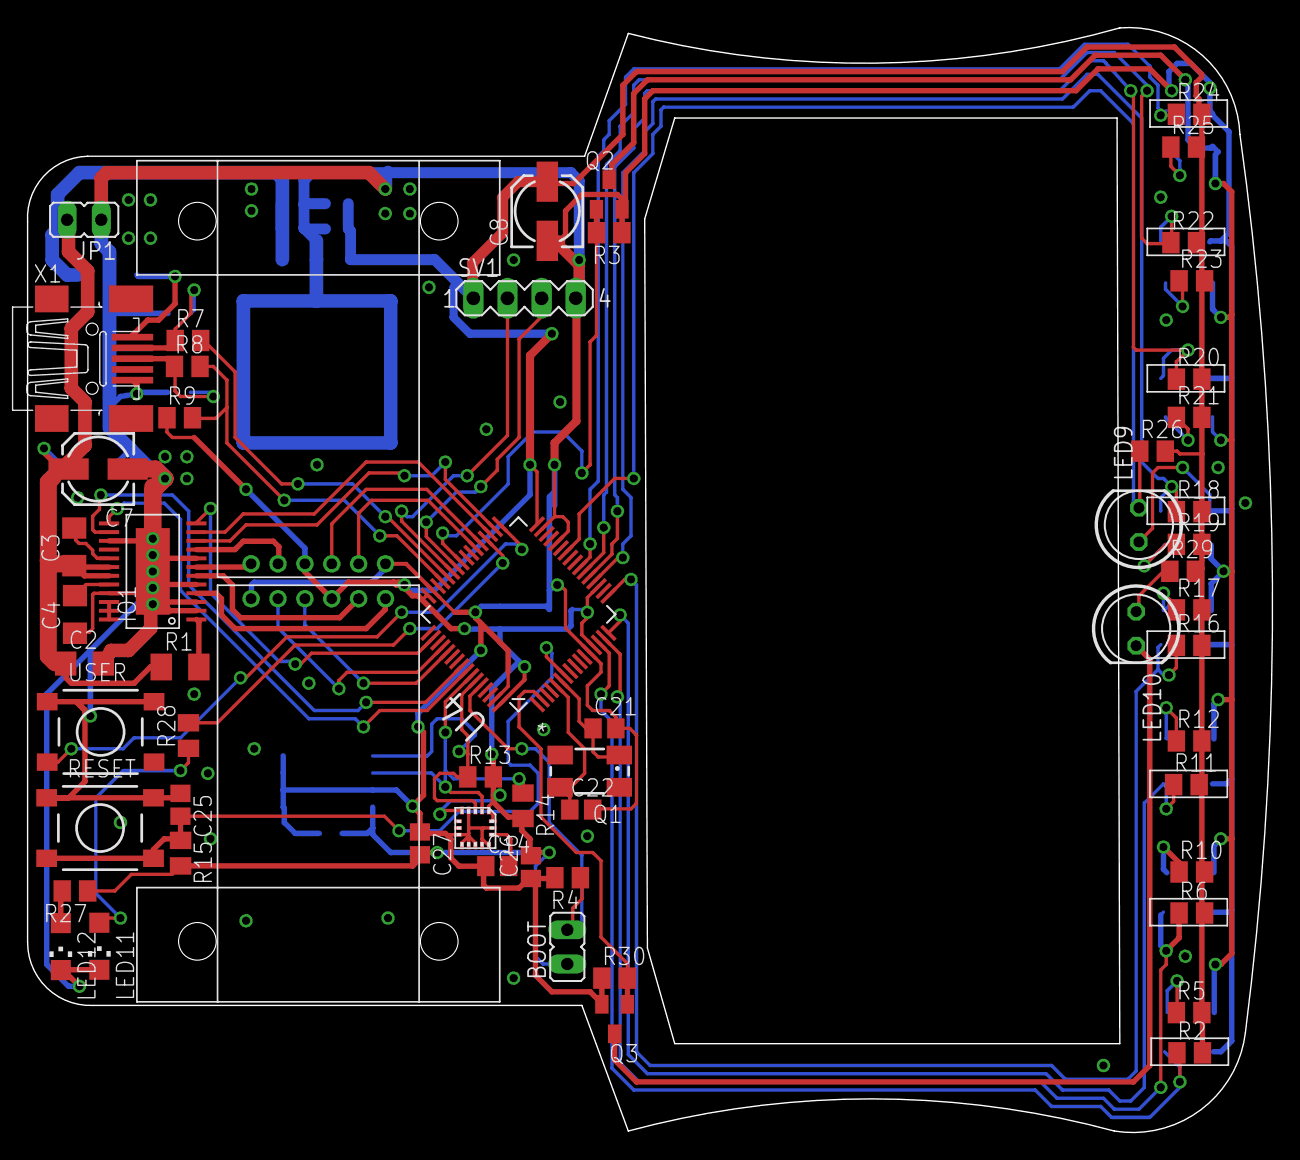
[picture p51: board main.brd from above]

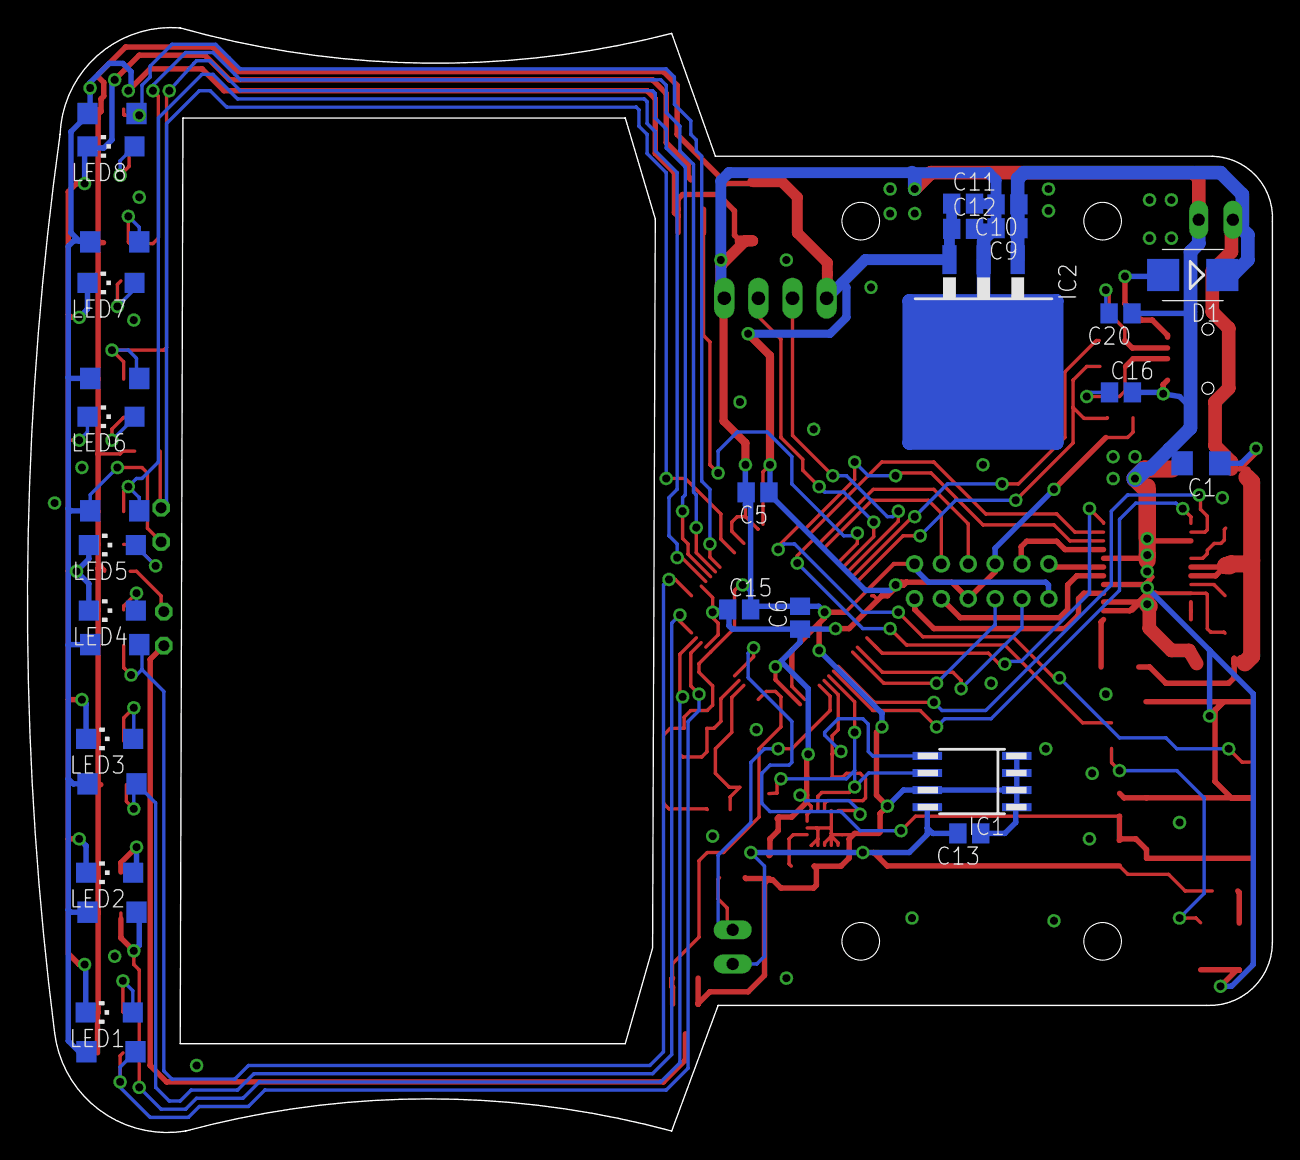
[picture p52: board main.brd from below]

Board: 2 copper layers, 92.6 x 82.2 mm, 89 parts (30 on the bottom side), 60 nets.

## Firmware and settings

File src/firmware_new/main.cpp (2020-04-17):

#include <embedded_libs.h>

#include <diagnostic.h>
#include <robot.h>

#include <movement.h>

int main()
{
    drivers.init();

    key.read();

    timer.delay_ms(1000);


    diagnostic();


    Robot robot;
    robot.main();

    /*
    Movement movement;

    movement.set(MOVEMENT_TURN_RIGHT, 100);
    movement.process();

    timer.delay_ms(500);

    movement.set(MOVEMENT_TURN_RIGHT, -100);
    movement.process();

    timer.delay_ms(500);

    movement.set(MOVEMENT_TURN_LEFT, 100);
    movement.process();

    timer.delay_ms(500);

    movement.set(MOVEMENT_TURN_LEFT, -100);
    movement.process();

    timer.delay_ms(500);
    */


    while (1)
    {
        timer.delay_ms(1000);
    }

}

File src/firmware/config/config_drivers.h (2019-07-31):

#ifndef _CONFIG_DRIVERS_H_
#define _CONFIG_DRIVERS_H_

#include <config_type.h>


#ifdef ROBOT_TYPE_MOTOKO_UPRINSING_1

//line sensor parameters
#define LINE_SENSOR_THRESHOLD   ((int)300)
//#define LINE_SENSOR_THRESHOLD   ((int)400)
//#define LINE_SENSOR_THRESHOLD   ((int)500)
#define LINE_SENSOR_DT          ((unsigned int)4)
#define LINE_SENSOR_STEP        ((int)128)


//distance sensor parameters
#define DISTANCE_DT             ((unsigned int)5)
#define DISTANCE_WARNING        ((float)0.85)
#define DISTANCE_OBSTACLE       ((float)0.7)


//imu dt in ms
#define IMU_DT                  ((unsigned int)10)
#define IMU_SINGLE_AXIS_MODE    false

//encoders parameters
#define PULSES_PER_ROTATION     ((int32_t)180)
#define WHEEL_CIRCUMFERENCE     ((int32_t)88)



//motor controll
#define MOTOR_CONTROLL_DT       LINE_SENSOR_DT

#define MOTOR_CONTROLL_SPEED_MAX         ((float)2000.0)


#define MOTOR_CONTROLL_PID_LEFT_KP    ((float)1.1)
#define MOTOR_CONTROLL_PID_LEFT_KI    ((float)0.09)
#define MOTOR_CONTROLL_PID_LEFT_KD    ((float)1.0)
#define MOTOR_CONTROLL_PID_RIGHT_KP   ((float)1.1)
#define MOTOR_CONTROLL_PID_RIGHT_KI   ((float)0.09)
#define MOTOR_CONTROLL_PID_RIGHT_KD   ((float)1.0)


#endif





#ifdef ROBOT_TYPE_MOTOKO_UPRINSING_2

//line sensor parameters
#define LINE_SENSOR_THRESHOLD   ((int)300)
//#define LINE_SENSOR_THRESHOLD   ((int)400)
//#define LINE_SENSOR_THRESHOLD   ((int)500)
#define LINE_SENSOR_DT          ((unsigned int)4)
#define LINE_SENSOR_STEP        ((int)64)


//distance sensor parameters
#define DISTANCE_DT             ((unsigned int)20)
#define DISTANCE_WARNING        ((float)0.7)
#define DISTANCE_OBSTACLE       ((float)0.65)

//imu dt in ms
#define IMU_DT                  ((unsigned int)10)
#define IMU_SINGLE_AXIS_MODE    false

//encoders parameters
#define PULSES_PER_ROTATION     ((int32_t)180)
#define WHEEL_CIRCUMFERENCE     ((int32_t)88)



//motor controll
#define MOTOR_CONTROLL_DT       LINE_SENSOR_DT

#define MOTOR_CONTROLL_SPEED_MAX         ((float)2000.0)


#define MOTOR_CONTROLL_PID_LEFT_KP    ((float)1.1)
#define MOTOR_CONTROLL_PID_LEFT_KI    ((float)0.09)
#define MOTOR_CONTROLL_PID_LEFT_KD    ((float)1.0)
#define MOTOR_CONTROLL_PID_RIGHT_KP   ((float)1.1)
#define MOTOR_CONTROLL_PID_RIGHT_KI   ((float)0.09)
#define MOTOR_CONTROLL_PID_RIGHT_KD   ((float)1.0)


#endif















#ifdef ROBOT_TYPE_MOTOKO_UPRINSING_3

//line sensor parameters
#define LINE_SENSOR_THRESHOLD   ((int)300)
#define LINE_SENSOR_DT          ((unsigned int)4)
#define LINE_SENSOR_STEP        ((int)64)
 

//distance sensor parameters
#define DISTANCE_DT             ((unsigned int)20)
#define DISTANCE_WARNING        ((float)0.7)
#define DISTANCE_OBSTACLE       ((float)0.65)

//imu dt in ms
#define IMU_DT                  ((unsigned int)10)
#define IMU_SINGLE_AXIS_MODE    true

//encoders parameters
#define PULSES_PER_ROTATION     ((int32_t)180)
#define WHEEL_CIRCUMFERENCE     ((int32_t)88)



//motor controll
#define MOTOR_CONTROLL_DT       LINE_SENSOR_DT

#define MOTOR_CONTROLL_SPEED_MAX         ((float)2000.0)


#define MOTOR_CONTROLL_PID_LEFT_KP    ((float)1.1)
#define MOTOR_CONTROLL_PID_LEFT_KI    ((float)0.09)
#define MOTOR_CONTROLL_PID_LEFT_KD    ((float)1.0)
#define MOTOR_CONTROLL_PID_RIGHT_KP   ((float)1.1)
#define MOTOR_CONTROLL_PID_RIGHT_KI   ((float)0.09)
#define MOTOR_CONTROLL_PID_RIGHT_KD   ((float)1.0)


#endif

#endif

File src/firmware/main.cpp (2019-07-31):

#include <embedded_libs.h>
#include <drivers/drivers.h>
#include <robot.h>

#include <diagnostic.h>

#include <movement.h>

int main()
{
    drivers.init();
    auto res = key.read();

    //diagnostic();
    //brick_avoid_test();

    Robot robot;

    if (res == 1)
        robot.mapping_enable();
    else
        robot.fast_run_enable();

    robot.main();
}

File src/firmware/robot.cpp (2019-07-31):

#include <robot.h>
#include <config_robot.h>
#include <movement.h>

class LineDetected: public MovementTerminateConditionInterface
{
    public:
        bool main()
        {
            if (line_sensor.result.line_lost_type == LINE_LOST_NONE)
                return true;

            return false;
        }
};

LineDetected line_detected;

Robot::Robot()
{
    mapping_enabled  = false;
    fast_run_enabled = false;

    //initialize steering PD controll
    steering_pid.init(STEERING_PID_KP, STEERING_PID_KI, STEERING_PID_KD, STEERING_PID_LIMIT);

    //speed rise limit
    speed_ramp.init(LINE_FOLLOWING_SPEED_RAMP_RISE);

    //initialize line curve type predictor using neural network
    line_predictor.init(cnn);

    int ignore_distance = 200;
    Array<int, MAX_OBSTACLES_COUNT> brick_detection_pattern;


    brick_detection_pattern[0] = BRICK_AVOID_SIDE_LEFT;
    brick_detection_pattern[1] = BRICK_AVOID_SIDE_RIGHT;
    brick_detection_pattern[2] = 0;
    brick_detection_pattern[3] = 0;
    brick_detection_pattern[4] = 0;
    brick_detection_pattern[5] = 0;
    brick_detection_pattern[6] = 0;
    brick_detection_pattern[7] = 0;


    brick_detection.init(brick_detection_pattern, ignore_distance);


    mapping_distance_next = 0;
    mapping_distance_prev = 0;
    line_mapping.init();
    //line_mapping.print_json();

    fast_run_max_distance = FAST_RUN_MAX_DISTANCE;
    bridge_active = false;
}

Robot::~Robot()
{

}



void Robot::main()
{
    while (1)
    {
        /*
        if (distance_sensor.ready() && brick_detection.process(distance_sensor.result) != 0)
        {
            allign_to_line(50);

            if (brick_detection.get() > 0)
                brick_avoid.avoid(BRICK_AVOID_SIDE_LEFT);
            else
                brick_avoid.avoid(BRICK_AVOID_SIDE_RIGHT);


            motor_controll.set_left_speed(0);
            motor_controll.set_right_speed(0);
            speed_ramp.set_speed(0.0);

            steering_pid.reset(line_sensor.result.center_line_position);
        }
        else
        */

        if (line_sensor.ready())
        {
            if (line_sensor.result.line_lost_type == LINE_LOST_NONE)
            {
                if (line_sensor.result.line_type == LINE_TYPE_SPOT)
                {
                    spot_move();

                    speed_ramp.set_speed(0);

                    steering_pid.reset(line_sensor.result.center_line_position);
                }
                else
                {
                    line_following();
                }
            }
            else
            {
                if (line_sensor.result.line_lost_type == LINE_LOST_CENTER)
                {
                    movement.init(&line_detected, 0, 280, 0.8, 0.8, 0.005, 0.005, motor_controll.get_speed_left(),  motor_controll.get_speed_right());
                    movement.process();
                }
                if (line_sensor.result.line_lost_type == LINE_LOST_LEFT)
                {
                    movement.init(&line_detected, 0, 250, 0.6, 0.6, 0.005, 0.005, 0,  motor_controll.get_speed_right()*0.5);
                    movement.process();
                }
                if (line_sensor.result.line_lost_type == LINE_LOST_RIGHT)
                {
                    movement.init(&line_detected, 250, 0, 0.6, 0.6, 0.005, 0.005, motor_controll.get_speed_left()*0.5,  0);
                    movement.process();
                }

            }
        }
    }
}


void Robot::line_following()
{
    //compute curve shape using CNN
    line_predictor.process(line_sensor.adc_result, encoder_sensor.get_distance());

    //set correct speed limit
    float speed_limit = LINE_FOLLOWING_SPEED_MIN;


    switch (line_predictor.get_result())
    {
      case   2: speed_limit = LINE_FOLLOWING_SPEED_MAX; break;
      case   1:
      case   3: speed_limit = (LINE_FOLLOWING_SPEED_MAX + LINE_FOLLOWING_SPEED_MIN)/2.0; break;
      default : speed_limit = LINE_FOLLOWING_SPEED_MIN; break;
    } 

    if (fast_run_enabled)
    {
        if (fast_run_max_distance < encoder_sensor.get_distance())
        {
            speed_limit = LINE_FOLLOWING_SPEED_MAX;

            int map_a = line_mapping.get_closest(encoder_sensor.get_distance());
            int map_b = line_mapping.get_closest(encoder_sensor.get_distance() + LINE_MAPPING_STEP);


            if ((map_a == 0)||(map_a == 4)||
                (map_b == 0)||(map_b == 4))
                speed_limit = LINE_FOLLOWING_SPEED_MIN;
        }
        else
        {
            fast_run_disable();
        }
    }

    if (line_sensor.result.line_type == LINE_TYPE_SPOT)
    {
        speed_limit = LINE_FOLLOWING_SPEED_MIN;
    }

    if (distance_sensor.result.front_obstacle_warning)
        speed_limit = LINE_FOLLOWING_SPEED_MIN;

    //compute next speed, using ramp and speed limit for this curve
    float speed = speed_ramp.process(speed_limit);

    //get line position and compute error
    float line_position = line_sensor.result.center_line_position;
    //float line_position = line_sensor.result.right_line_position;

    float error         = 0.0 - line_position;

    //compute steering using PID
    float steering = steering_pid.process(error, line_position);

    //compute outputs for motors
    float speed_left  = steering  + speed;
    float speed_right = -steering + speed;

    //input into PID controllers for motors
    motor_controll.set_left_speed(speed_left);
    motor_controll.set_right_speed(speed_right);

    //set last line position for lost line search
    //line_search.set_last_line_position(line_position);

    if (mapping_enabled)
    {
        /*
        unsigned int line_type = line_predictor.get_result();
        int mapping_distance_now = encoder_sensor.get_distance();

        if (mapping_distance_now >= mapping_distance_next)
        {
            int dist_dif = mapping_distance_now - mapping_distance_prev;
            mapping_distance_prev = mapping_distance_now;

            if (dist_dif > 255)
                dist_dif = 255;
            if (dist_dif < 0)
                dist_dif = 0;

            int line_position_ = (line_position + 1.0)*100;
            if (line_position_ > 255)
                line_position_ = 255;
            if (line_position_ < 0)
                line_position_ = 0;

            line_mapping.add(dist_dif, line_position_);

            mapping_distance_next+= LINE_MAPPING_STEP;
        }
        */
    }
}
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

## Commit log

2018-09-06 initial drivers test
2018-09-07 motor driver
2018-09-08 motor controll - not tested yet
2018-09-08 motor controll
2018-09-24 robot gui
    [model.obj]
2019-03-26 network test
    [embedded_net_speed_test.ods, embedded_net_speed_test.xlsx]
2019-04-20 filter + eeprom
    [motoko_sensor_shield.stl]
2019-04-27 new line sensor driver
2019-05-05 line scan camera tests
    [model.obj]
2019-05-17 line scan camera net
2019-06-04 new board
    [main_3_0.brd, main_3_0.sch]
2019-06-21 board v4
    [motoko_4_0.brd, motoko_4_0.sch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]
2019-06-25 bom + board outline
    [bill_of_material.ods]
2019-06-25 laser test
    [model.obj]
2019-07-12 new gyro tests
2019-07-19 gyro tests
    [model.obj]
2020-04-14 visualisation python
    [model.obj]
2021-03-13 new hardware
    [motoko_5_0.brd, motoko_5_0.sch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]

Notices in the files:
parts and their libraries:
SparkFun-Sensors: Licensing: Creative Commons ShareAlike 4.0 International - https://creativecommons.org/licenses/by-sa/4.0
